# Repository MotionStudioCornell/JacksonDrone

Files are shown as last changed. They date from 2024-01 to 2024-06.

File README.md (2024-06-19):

# JacksonDrone

For the build guide, documentation, and more, please check out our [Wiki page](https://github.com/MotionStudioCornell/JacksonDrone/wiki).

<p align="center">
P3
</p>

# Getting Started

Clone the project
```
git clone https://github.com/MotionStudioCornell/JacksonDrone.git
```

Go to the software dir.
```
cd JacksonDrone && cd software
```

Build the project

```
./builder
```

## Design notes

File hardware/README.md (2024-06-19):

# Schematics
KiCad Schematics

*Note: please export the schematics to `P2.svg` so this README can preview it correctly*

The controller software can be found here: https://github.com/MotionStudioCornell/P2

P2-Schematics

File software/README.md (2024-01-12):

# P2 Flight Controller

Custom Pico-based flight controller/computer software.

The KiCad Schematics can be found here: https://github.com/MotionStudioCornell/P2-Schematics

## Dev Info

### MPU9250
Data Sheet: https://invensense.tdk.com/wp-content/uploads/2015/02/PS-MPU-9250A-01-v1.1.pdf

Register Map: https://invensense.tdk.com/wp-content/uploads/2015/02/MPU-9250-Register-Map.pdf

### Pi Pico(W)
Documents: https://www.raspberrypi.com/documentation/microcontrollers/c_sdk.html

## Build

Requirement:

Raspberry Pi Pico C/C++ SDK

`cd build`

`cmake ../src -DPICO_BOARD=pico_w`

`make`

## Flash

Find `P2.uf2` in the `build` folder, and drag it onto the Pico MSD(Or any methods you prefer)

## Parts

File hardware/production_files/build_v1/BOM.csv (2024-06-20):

Designator | Footprint | Comment
C3 | C_0805_2012Metric | 0.1uF
C2 | C_0805_2012Metric | 10uF
L1 | L_Abracon_ASPI-4030S | 4.7uH
Regulator1 | TSOT-23-6 | AP63203WU
C4,C5 | C_0805_2012Metric | 22uF

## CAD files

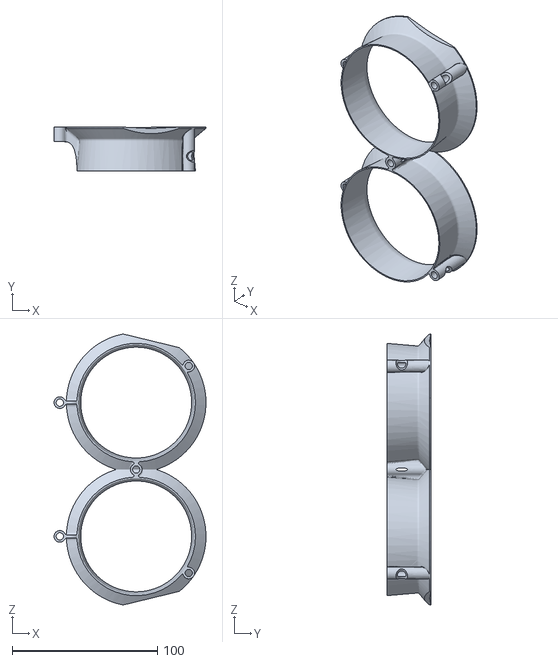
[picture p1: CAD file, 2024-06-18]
frame/guard.stl
104.5 x 30.0 x 186.3

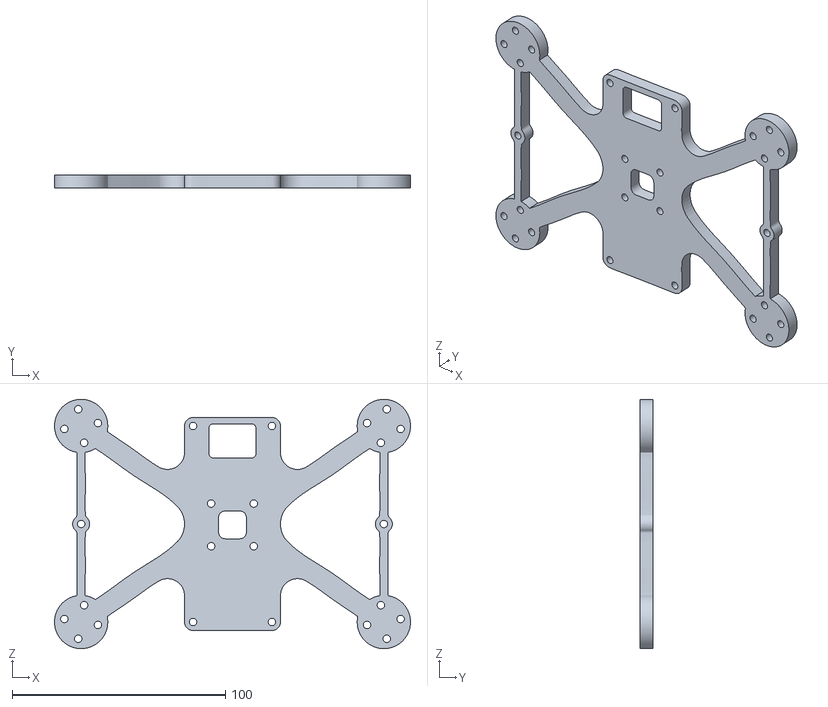
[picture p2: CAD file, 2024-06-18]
frame/buttom-plate.stl
167.0 x 6.00 x 116.9

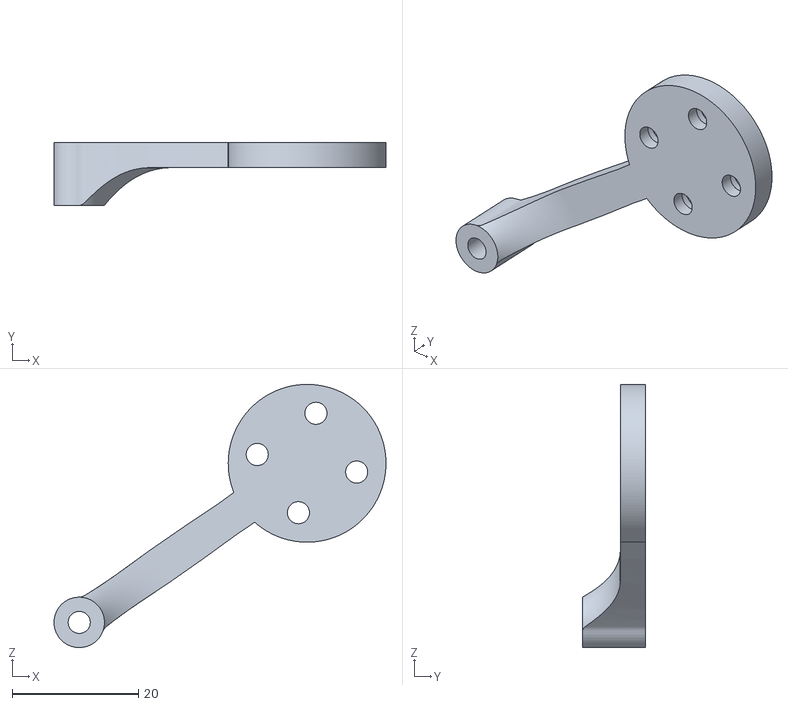
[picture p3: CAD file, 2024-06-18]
frame/gurad-extend.stl
52.6 x 10.0 x 41.7

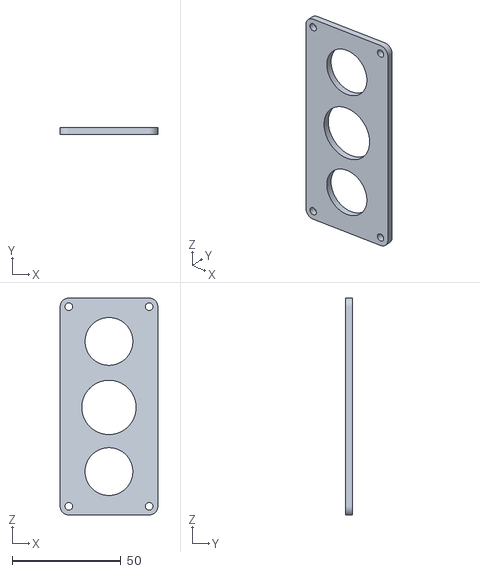
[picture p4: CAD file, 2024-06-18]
frame/top-plate.stl
45.0 x 3.00 x 99.9

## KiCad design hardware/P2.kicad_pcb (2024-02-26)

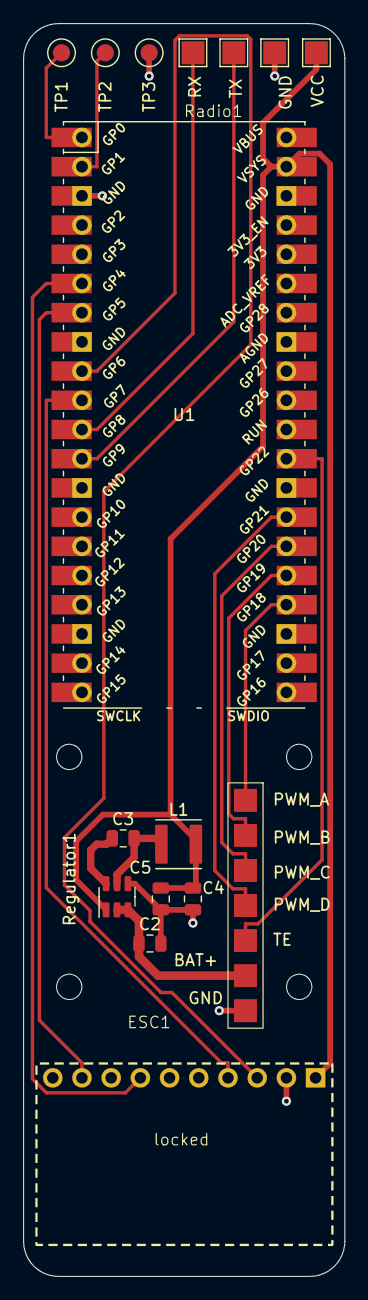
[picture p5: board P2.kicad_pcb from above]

Board: 2 copper layers, 27.9 x 109.0 mm, 17 parts (0 on the bottom side), 18 nets.

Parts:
C2: 10uF; C_0805_2012Metric
C3: 0.1uF; C_0805_2012Metric
C4, C5: 22uF; C_0805_2012Metric
ESC1: ESC
H1, H2, H3, H4: MountingHole; MountingHole_2.2mm_M2
L1: 4.7uH; L_Abracon_ASPI-4030S
Radio1: Radio
Regulator1: AP63203WU; TSOT-23-6
TP1: TX0; TestPoint_Pad_D2.0mm
TP2: TX1; TestPoint_Pad_D2.0mm
TP3: GND; TestPoint_Pad_D2.0mm
U1: Pico; RPi_Pico_SMD_TH
locked: MPU9250-Breakout

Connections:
+3V3: C4.1, C5.1, L1.2, Radio1.1 (VCC), Regulator1.1 (FB), U1.39 (VSYS), locked.1 (VCC)
+BATT: C2.1, ESC1.5 (BAT+), Regulator1.2 (EN), Regulator1.3 (IN)
/CS: U1.7 (GPIO5), locked.9 (NCS)
/MISO: U1.6 (GPIO4), locked.7 (ADO)
/MOSI: U1.10 (GPIO7), locked.4 (SDA)
/PWM_A: ESC1.1 (PWM_A), U1.24 (GPIO18)
/PWM_B: ESC1.2 (PWM_B), U1.25 (GPIO19)
/PWM_C: ESC1.3 (PWM_C), U1.26 (GPIO20)
/PWM_D: ESC1.4 (PWM_D), U1.27 (GPIO21)
/RX: Radio1.3 (TX), U1.12 (GPIO9)
/SCK: U1.9 (GPIO6), locked.3 (SCL)
/TE: ESC1.6 (TE), U1.29 (GPIO22)
/TX: Radio1.4 (RX), U1.11 (GPIO8)
GND: C2.2, C4.2, C5.2, ESC1.7 (GND), Radio1.2 (GND), Regulator1.4 (GND), TP3.1, U1.3 (GND), locked.2 (GND)
unnamed: C3.1, Regulator1.6 (BST)
unnamed: C3.2, L1.1, Regulator1.5 (SW)
unnamed: TP1.1, U1.1 (GPIO0)
unnamed: TP2.1, U1.2 (GPIO1)

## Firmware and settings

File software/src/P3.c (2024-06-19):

#include <stdio.h>
#include <stdlib.h>
#include "pico/stdlib.h"
#include "hardware/spi.h"
#include "hardware/pwm.h"
#include "hardware/uart.h"
#include "hardware/irq.h"
#include "pico/binary_info.h"
#include "../lib/MPU9250/mpu9250.h"
#include "../lib/ESC/esc.h"
#include "../lib/Filter/leaky_LP.h"
#include "../lib/Control/controller.h"
#include "../lib/Radio/radio.h"
#include "pico/cyw43_arch.h"
#include <math.h>
#include <time.h>

// Connection
// GPIO 4(pin 6)MISO / spi0_rx→ ADO on MPU9250 board
// GPIO 5(pin 7)Chip select → NCS on MPU9250 board
// GPIO 6(pin 9)SCK / spi0_sclk → SCL on MPU9250 board
// GPIO 7(pin 10)MOSI / spi0_tx → SDA on MPU9250 board
// IMU const
#define PIN_MISO 4
#define PIN_CS 5
#define PIN_SCK 6
#define PIN_MOSI 7

// ESC const
#define PWM_WRAP 100000 // counts
#define PWM_FREQ 50     // hz
#define MAX_DUTY 0.1
#define MIN_DUTY 0.05

#define PIN_PWM1 21
#define PIN_PWM2 20
#define PIN_PWM3 19
#define PIN_PWM4 18

// uart0
#define UART_ID uart0
#define DATA_BITS 8
#define STOP_BITS 1
#define PARITY UART_PARITY_NONE

// RADIO
#define RADIO_TX 8
#define RADIO_RX 9

// controller
 #define Default_Kp 0.2
 #define Default_Ki 10
 #define Default_Kd 0.015
 


#define Default_yaw_Kp 0
#define Default_yaw_Ki 0
#define Default_yaw_Kd 0


// init throttle when armed, so it doesnt start weird
#define INIT_THROTTLE 15

static mpu9250 imu;
static ESC esc;
// Low pass
static leaky_lp w_filter;
static leaky_lp a_filter;
// controller
static controller fc;
// radio
static radio rdo;

// control cycle timing
#define dT_ms 20
#define dT_s dT_ms / 1000.0

volatile int buffer_index = 0;
volatile bool new_input = true;

void uart0_setup()
{
  // Set up our UART with a basic baud rate.
  uart_init(UART_ID, 115200);

  gpio_set_function(0, GPIO_FUNC_UART);
  gpio_set_function(1, GPIO_FUNC_UART);

  uart_set_baudrate(UART_ID, 115200);
  // Set UART flow control CTS/RTS, we don't want these, so turn them off
  uart_set_hw_flow(UART_ID, false, false);
  // Set our data format
  uart_set_format(UART_ID, DATA_BITS, STOP_BITS, PARITY);
  // Turn off FIFO's - we want to do this character by character
  uart_set_fifo_enabled(UART_ID, false);
}

// kp=x, kd=y, in serial to set values
void PD_handler()
{
  static char buffer[32];
  static int buffer_index = 0;
  char ch;
  new_input = true;

  while (uart_is_readable(uart0))
  {
    // Read a single character
    ch = uart_getc(uart0);

    // Check for buffer overflow
    if (buffer_index < (sizeof(buffer) - 1))
    {
      // If the character is not a newline or carriage return, add it to the buffer
      if (ch != '\n' && ch != '\r')
      {
        buffer[buffer_index++] = ch;
      }
      else
      {
        buffer[buffer_index] = '\0'; // Null-terminate the string

        // Check if the input is for kp
        if (strncmp(buffer, "kp=", 3) == 0)
        {
          fc.Kp = atof(buffer + 3); // Convert the string to a number and assign to kp
        }

        // Check if the input is for ki
        if (strncmp(buffer, "ki=", 3) == 0)
        {
          fc.Ki = atof(buffer + 3); // Convert the string to a number and assign to kp
        }
        // Check if the input is for kd
        else if (strncmp(buffer, "kd=", 3) == 0)
        {
          fc.Kd = atof(buffer + 3); // Convert the string to a number and assign to kd
        }

        buffer_index = 0; // Reset the buffer index
      }
    }
    else
    {
      // Handle buffer overflow, for example, by clearing the buffer
      buffer_index = 0;
    }
  }
}
int main()

{
  // Serial
  stdio_init_all();

  // UART
  uart0_setup();
  // And set up and enable the interrupt handlers
  irq_set_exclusive_handler(UART0_IRQ, PD_handler);
  irq_set_enabled(UART0_IRQ, true);
  // Now enable the UART to send interrupts - RX only
  uart_set_irq_enables(UART_ID, true, false);

  // Need Wifi For the LED GPIO
  if (cyw43_arch_init())
  {
    printf("Wi-Fi init failed");
    return -1;
  }
  // Turn on the LED to show we are powered on
  cyw43_arch_gpio_put(CYW43_WL_GPIO_LED_PIN, 1);
  // RADIO
  radio_setup(&rdo, RADIO_RX, RADIO_TX);

  // IMU stuff
  mpu9250_setup(&imu, PIN_CS, PIN_MISO, PIN_SCK, PIN_MOSI);
  printf("Calibrating Gyro....Keep it Still...\n");
  gyro_cal(&imu, 50);
  acc_cal(&imu, 50);
  printf("Done. Offsets: w_x: %.5f, w_y:%.5f, w_z:%.5f \n", imu.w_offsets[0], imu.w_offsets[1], imu.w_offsets[2]);

  // ESC stuff
  uint32_t PWM_PIN[4] = {PIN_PWM1, PIN_PWM2, PIN_PWM3, PIN_PWM4};
  esc_setup(&esc, PWM_PIN, PWM_FREQ, PWM_WRAP, MIN_DUTY, MAX_DUTY);

  printf("Calibrating ESC...\n");
  cali_motor(&esc);
  printf("Done.\n");

  printf("Arming ESC...\n");
  arm_motor(&esc);
  printf("Done.\n");

  leaky_init(&w_filter, 0.9f);
  leaky_init(&a_filter, 0.9f);

  init_controller(&fc, 0.98f, dT_s, Default_Kp, Default_Ki, Default_Kd, Default_yaw_Kp, Default_yaw_Ki, Default_yaw_Kd);

  // blink to show we are ready
  cyw43_arch_gpio_put(CYW43_WL_GPIO_LED_PIN, 1);
  sleep_ms(100);
  cyw43_arch_gpio_put(CYW43_WL_GPIO_LED_PIN, 0);
  sleep_ms(100);
  cyw43_arch_gpio_put(CYW43_WL_GPIO_LED_PIN, 1);

  while (1)
  {
    absolute_time_t startTime = get_absolute_time();
    // fetch new imu data
    mpu9250_update(&imu);
    float wf[3];
    float af[3];
    // low pass
    leaky_update(&w_filter, imu.w, wf);
    leaky_update(&a_filter, imu.a, af);

    // good for arduino serial plotter:
    //  printf("wx:%f, wy:%f, wz:%f, wxf:%f, wyf:%f, wzf:%f, ax:%f, ay:%f, az:%f, axf:%f, ayf:%f, azf:%f\n",
    //         imu.w[0], imu.w[1], imu.w[2],
    //         wf[0], wf[1], wf[2],
    //         imu.a[0], imu.a[1], imu.a[2],
    //         af[0], af[1], af[2]);

    update_controller(&fc, wf, af);

    
    // displays the current throttle
    if (new_input)
    {
      new_input = false;
      printf("roll:%.3f, pitch:%.3f, yaw:%.3f \n", fc.x.roll, fc.x.pitch, fc.x.yaw);
      printf("Kp = %.3f, Ki = %.3f, Kd = %.3f, throttle = %.3f , %s\n", fc.Kp, fc.Ki, fc.Kd, rdo.throttle, rdo.controller_armed ? "ARMed" : "NOT-ARMed");
    }

    if (rdo.controller_armed)
    {
      motor_control(&esc, INIT_THROTTLE + rdo.throttle + fc.u.t1, 1);
      motor_control(&esc, INIT_THROTTLE + rdo.throttle + fc.u.t2, 2);
      motor_control(&esc, INIT_THROTTLE + rdo.throttle + fc.u.t3, 3);
      motor_control(&esc, INIT_THROTTLE + rdo.throttle + fc.u.t4, 4);
      
    }
    else
    {
      motor_control(&esc, 0, 1);
      motor_control(&esc, 0, 2);
      motor_control(&esc, 0, 3);
      motor_control(&esc, 0, 4);
    }

    absolute_time_t endTime = get_absolute_time();

    int64_t time_diff_ms = absolute_time_diff_us(startTime, endTime) / 1000;
    // to achieve a fixed control loop time, if possible
    u_int32_t sleep_time_ms = dT_ms - time_diff_ms > 0 ? dT_ms - time_diff_ms : 0;
    sleep_ms(sleep_time_ms);
    // printf("cycle time: %lld ms, ", time_diff_ms <= dT_ms ? dT_ms : time_diff_ms);
    // print_control(fc.u);
  }
}

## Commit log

2024-02-25 update sche
    [P2.kicad_pcb, P2.kicad_sch]
2024-02-25 add radio
    [P2.kicad_sch]
2024-02-25 pre-pcb design
    [P2.kicad_sch]
2024-02-26 pcb done
    [P2-B_Cu.gbr, P2-B_Mask.gbr, P2-B_Paste.gbr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]
2024-02-26 change pkg
    [BOM.csv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]
2024-02-26 update svg
    [P2.kicad_sch]
2024-03-06 builder scripter
    [P2.kicad_sch]
2024-03-10 Low pass filter
2024-03-19 complementry filter lib
    [BOM.csv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]
2024-03-23 P for roll and pitch, motor bug
    [BOM.csv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]
2024-03-23 fix motor issue
2024-03-26 serial throttle change
2024-04-16 init arm throttle
2024-04-24 yaw control
2024-06-20 pcb v1, and production files
    [BOM.csv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]
